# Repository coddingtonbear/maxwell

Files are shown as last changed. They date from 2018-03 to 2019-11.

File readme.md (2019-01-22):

# Maxwell: Bicycle Electrification



See my little blog post about this here: [http://coddingtonbear.net/maxwell-bicycle-electrification/](http://coddingtonbear.net/maxwell-bicycle-electrification/).

I have a bicycle dynamo on my bike, a rudimentary understanding of electronics, and a bunch of neopixels, gps, and bluetooth modules to use.  This is what happens when those things combine.

Maxwell is a two-part bike computer I've designed to allow me to do a few things:

* Light and control neopixel LEDs wrapped around my bike for added safety while biking at night, and added fun when biking with groups.
* Charge an easily-swappable 18650 Li-On cell for potential use when bike touring.
* Gather and transmit GPS coordinates for display on the internet somewhere.
* Display status information including my current speed, battery voltage, and current consumption, as well as disable or enable bike features including, most importantly, disabling and enabling the LEDs from a small screen mounted at the front of the bike.
* Send interesting data for display on the internet for completely impractical reasons.

The "remote" unit is based around the STM32F103CB microcontroller, and the "base" unit is based around its slightly-more-full-featured brother, the STM32F103RE.  Both communicate with one another over a CANBus (routed through two of the conductors in a length of ethernet cable) to share status information and emit/handle commands.




## Schematics

### Main





### LTE Module



### Head Unit (Remote)




## Errata

Checked items indicate errata that have been corrected in the schematic.

### Maxwell

None as of rev 1.7.

### Maxwell-remote

* [ ] Incorrect diode footprint for polarity protection.  There also might be a power deliver problem through those diodes.  Investigate that the selected mosftet is ON at Vgs -3.3.
* [ ] I think the gerbers I generated originally may have excluded the rear solder mask, as the resistors and vias were covered.
* [ ] Board-to-board interconnect should probably either not use an FPC connector, or use multiple conductors for power/ground.  I had to build a workaround connector for transferring power between the two boards.
* [ ] Resistor R2 of maxwell-remote-2 isn't really necessary; it could be connected directly to VCC.

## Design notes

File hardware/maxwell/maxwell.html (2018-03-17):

# BOM Rev

Date

Company

Comment 1

Comment 2

Comment 3

Comment 4

Total Parts

# 82 (Unique 56)

Ref

Qty

Value

Footprint

Datasheet

[BZ] -

BZ1

1

Buzzer

coddingtonbear/coddingtonbear.pretty:12mm_buzzer

[C] -

C1 C2 C3

3

2.2u

coddingtonbear:CP_Tantalum_Case-C_EIA-6032-28_Milling

C4 C5

2

0.1u

coddingtonbear/coddingtonbear.pretty:0805_Milling

C6 C7 C8 C9

4

22p

coddingtonbear/coddingtonbear.pretty:0805_Milling

C10 C11 C12 C13

4

100n

coddingtonbear/coddingtonbear.pretty:0805_Milling

C14

1

220u

coddingtonbear:CP_Tantalum_Case-C_EIA-6032-28_Milling

C15

1

100u

coddingtonbear:CP_Tantalum_Case-D_EIA-7343-31_Milling

C17

1

0.1

fruchti/fruchtilib/mod/rcl.pretty:CP_13mm_200

C18

1

100nF

coddingtonbear/coddingtonbear.pretty:0805_Milling

[D] -

D1

1

GS1M-LTP

mcous/kicad-lib/footprints/diode.pretty:DO-214AC

D2 D3

2

18

adamgreig/agg-kicad/agg.pretty:DO-214AA-SMB

D4

1

MB24S

coddingtonbear/coddingtonbear.pretty:SO-4_Milling

[J] -

J1

1

Canbus 1

coddingtonbear/coddingtonbear.pretty:JST_XH_B05B-XH-A_05x2.50mm_Straight_LargePads

J2

1

Canbus 2

coddingtonbear/coddingtonbear.pretty:JST_XH_B05B-XH-A_05x2.50mm_Straight_LargePads

J3

1

Neopixel

coddingtonbear/coddingtonbear.pretty:JST_XH_B03B-XH-A_03x2.50mm_Straight_LargePads

J4

1

BOOT0

coddingtonbear:Pin_Header_Straight_1x02_Pitch1.27mm_JMP

J5

1

SPI2_A

coddingtonbear/coddingtonbear.pretty:JST_XH_B06B-XH-A_06x2.50mm_Straight_LargePads

J6

1

Programmer

KiCad/Pin_Headers.pretty:Pin_Header_Straight_1x04_Pitch2.54mm

J7

1

Dynamo Input

coddingtonbear/coddingtonbear.pretty:JST_XH_B02B-XH-A_02x2.50mm_Straight_LargePads

J8

1

BOOT1

coddingtonbear:Pin_Header_Straight_1x02_Pitch1.27mm_JMP

J9

1

Battery

coddingtonbear/coddingtonbear.pretty:JST_XH_B02B-XH-A_02x2.50mm_Straight_LargePads

J10

1

SPI2_B

coddingtonbear/coddingtonbear.pretty:JST_XH_B06B-XH-A_06x2.50mm_Straight_LargePads

J11

1

BACKUP

coddingtonbear/coddingtonbear.pretty:JST_XH_B02B-XH-A_02x2.50mm_Straight_LargePads

J12

1

UART4

coddingtonbear/coddingtonbear.pretty:JST_XH_B04B-XH-A_04x2.50mm_Straight_LargePads

J13

1

UART5

coddingtonbear/coddingtonbear.pretty:JST_XH_B04B-XH-A_04x2.50mm_Straight_LargePads

J14

1

I2C1

coddingtonbear/coddingtonbear.pretty:JST_XH_B04B-XH-A_04x2.50mm_Straight_LargePads

J15

1

GPIO

KiCad/Pin_Headers.pretty:Pin_Header_Straight_1x03_Pitch2.54mm

[Q] -

Q1

1

BSS138

coddingtonbear/coddingtonbear.pretty:SOT-23_LargePads

Q2

1

PSMN5R4-25YLD

coddingtonbear/coddingtonbear.pretty:PSMN5R4-25YLD

Q3 Q4 Q5

3

NTR1P02T1

coddingtonbear/coddingtonbear.pretty:SOT-23_LargePads

[R] -

R1 R6 R7 R8 R10 R13 R28 R35

8

10k

coddingtonbear/coddingtonbear.pretty:0805_Milling

R2 R16

2

2.2k

coddingtonbear/coddingtonbear.pretty:0805_Milling

R3 R29 R31

3

330

coddingtonbear/coddingtonbear.pretty:0805_Milling

R4

1

>35

coddingtonbear/coddingtonbear.pretty:0805_Milling

R5 R9

2

100k

coddingtonbear/coddingtonbear.pretty:0805_Milling

R11

1

50

coddingtonbear/coddingtonbear.pretty:0805_Milling

R12

1

16-17k

coddingtonbear/coddingtonbear.pretty:0805_Milling

R14

1

200

coddingtonbear/coddingtonbear.pretty:0805_Milling

R19

1

2k

coddingtonbear/coddingtonbear.pretty:0805_Milling

R20 R21 R23 R24

4

ANY

coddingtonbear/coddingtonbear.pretty:0805_Milling

R22

1

0.02

coddingtonbear/coddingtonbear.pretty:0805_Milling

R33

1

1M

coddingtonbear/coddingtonbear.pretty:0805_Milling

R34

1

110k

coddingtonbear/coddingtonbear.pretty:0805_Milling

R37

1

120

coddingtonbear/coddingtonbear.pretty:0805_Milling

[U] -

U1

1

MCP1501

adamgreig/agg-kicad/agg.pretty:SOT-23-6

U2

1

SN65HVD233

adamgreig/agg-kicad/agg.pretty:SOIC-8

U3

1

ITEAD_HC-05

pelrun/libKiCad/footprint/w_rf_modules.pretty:ITEAD_HC-05

U5

1

ESP-32S

coddingtonbear/coddingtonbear.pretty:ESP-32S

U6

1

FGPMMOPA6C

coddingtonbear/coddingtonbear.pretty:FGPMMOPA6C

U7

1

STM32F103RETx

kicad-castellated-breakouts:QFP64-1.27MM-CASTELLATED

U8

1

TLP188

coddingtonbear/coddingtonbear.pretty:SO-4_Milling

U9

1

Buck Regulator

coddingtonbear/coddingtonbear.pretty:BOOST_LM2596_3A

U10

1

MIC39102

adamgreig/agg-kicad/agg.pretty:SOIC-8

[U*] -

U*NaN

1

MCP73831T

apexelectrix/apex-smd.pretty:SOT-23-5

[Y] -

Y1

1

32.768k

KiCad/Crystals.pretty:Crystal_SMD_SeikoEpson_MC306-4pin_8.0x3.2mm

Y2

1

8M

nqbit/NQBit.pretty:HC-49USX_SMD

# BOM made with KICAD_BOM_WIZARD (https://github.com/HashDefineElectronics/KiCad_BOM_Wizard) (Generated Thursday, March 01, 2018 'PMt' 10:14:26 PM)

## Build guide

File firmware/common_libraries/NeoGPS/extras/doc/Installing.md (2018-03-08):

Installing
==========

1. [Download the library](#1-download-the-library)
2. [Choose a serial port](#2-choose-a-serial-port)
3. [Connect the GPS device](#3-connect-the-gps-device)
4. [Review `GPSport.h`](#4-review-librariesneogpssrcgpsporth)
5. [Open the example](#5--open-the-example-sketch-nmeaino)
6. [Build and upload](#6--build-and-upload-the-sketch-to-your-arduino)
<hr>

### 1. Download the library

It is easiest to use the [Ardino IDE Library Manager](https://www.arduino.cc/en/Guide/Libraries#toc3) to automatically download and install NeoGPS.  Select the menu **Sketch -> Include Library -> Manage Libraries**.  Then type "NeoGPS" in the Search box.

If you need to perform a manual installation,:

* Download the [master ZIP file](https://github.com/SlashDevin/NeoGPS/archive/master.zip).
*  Open the zip file and open the nested `NeoGPS-master` subdirectory.
*  Select and copy all files in the `NeoGPS-master` subdirectory into a new `Arduino/Libraries/NeoGPS` directory, like most libraries.  The `Arduino/Libraries/NeoGPS` directory should contain:<br>
```
extras
examples
src
library.properties
LICENSE
README.md
```

<hr>

### 2. Choose a serial port

**BEST**: The fastest, most reliable way to connect a GPS device is to use a HardwareSerial port.

On any Arduino board, you can connect the GPS device to the `Serial` pins (0 & 1).  You can still print debug statements, and they will show up on the Serial Monitor window.  The received GPS characters will not interfere with those prints, and you will not see those characters on the Serial Monitor window.

However, when you need to upload a new sketch to the Arduino over USB, **you must disconnect the GPS TX from the Arduino RX pin 0.**  Otherwise, the GPS characters will interfere with the upload data.  Some people put a switch in that connection to make it easy to upload without disturbing the wires.

For Mega, Due and Teensy boards, you can connect the GPS device to the `Serial1`,  `Serial2` or `Serial3` pins.

For Micro and Leo (and other 32U4-based Arduinos), you can connect the GPS device to the `Serial1` pins.

**2nd Best**:  If you can't connect the GPS device to a `HardwareSerial` port, you should download and install the [AltSoftSerial](https://github.com/PaulStoffregen/AltSoftSerial) or [NeoICSerial](https://github.com/SlashDevin/NeoICSerial) library.  These libraries only work on two specific pins (8 & 9 on an UNO).  This library is very efficient and reliable.  It uses one of the hardware TIMERs, so it may conflict with libraries that use TIMERs or PWM output (e.g., servo).

**3rd Best**:  If you can't use the pins required by `AltSoftSerial`, and your GPS device runs at 9600, 19200 or 38400 baud, you should download and install the [NeoSWSerial](https://github.com/SlashDevin/NeoSWSerial) library.  This library is almost as efficient.  It will help you avoid common timing problems caused by `SoftwareSerial`.  It does not need an extra TIMER, so it can be used with most other libraries.  It does use Pin Change Interrupts, but there is an option in the header file that allows you to coordinate other PCI usage with `NeoSWSerial`.

`NeoSWSerial` can be used with `AltSoftSerial` at the same time, allowing your sketch to have two extra serial ports.

**WORST**:  `SoftwareSerial` is NOT RECOMMENDED, because it disables interrupts for long periods of time.  This can interfere with other parts of your sketch, or with other libraries.  It cannot transmit and receive at the same time, and your sketch can only receive from one `SoftwareSerial` instance at time.

<hr>

### 3. Connect the GPS device

Most GPS devices are 3.3V devices, and most Arduinos are 5V devices.  Although many GPS modules are described as "3V & 5V compatible", 

<p align=center><b>YOU SHOULD NOT CONNECT A 5V ARDUINO TRANSMIT PIN TO THE 3.3V GPS RX PIN</b></p>

This can damage the device, cause overheating, system power problems or decrease the lifetime of battery-operated systems.  You must level-shift this connection with inexpensive level-shifting modules (best) or a resistor divider.

Connecting the 3.3V GPS TX pin to a 5V Arduino receive pin will not damage the GPS device, but it may not be reliable.  This is because the GPS TX voltage is slightly lower than what the Arduino requires.  It works in many situations, but if you are not able to receive GPS characters reliably, you probably need to use a level-shifting module (best) or a diode+resistor to "pull up" the GPS TX pin voltage.

<hr>

### 4. Review `Libraries/NeoGPS/src/GPSport.h`

This file declares a the serial port to be used for the GPS device.  You can either:

* Use the default `GPSport.h` and connect your GPS device according to what it chooses; or
* Replace the entire contents of `GPSport.h` and insert your own declarations (see below and comments in `GPSport.h`).

#### Default choices for GPSport.h

By default, Mega, Leonardo, Due, Zero/MKR1000 and Teensy boards will use `Serial1`.

All other Boards will use [AltSoftSerial](https://github.com/PaulStoffregen/AltSoftSerial) on two specific pins (see table at linked page).

If you want to use a different serial port library (review step 2 above), you must edit these `#include` lines in `GPSport.h`:

```
  //#include <NeoHWSerial.h>    // NeoSerial or NeoSerial1 for INTERRUPT_PROCESSING
  #include <AltSoftSerial.h>    // <-- DEFAULT.  Two specific pins required (see docs)
  //#include <NeoICSerial.h>    // AltSoftSerial with Interrupt-style processing
  //#include <NeoSWSerial.h>    // Any pins, only @ 9600, 19200 or 38400 baud
  //#include <SoftwareSerial.h> // NOT RECOMMENDED!
```

Uncomment **one** of those include statements, and it will use that library for the GPS serial port.

If you uncomment the `NeoSWSerial.h` include, pins 3 and 4 will be used for the GPS.  If your GPS is on different pins, you must edit these `#define` lines in `GPSport.h`:

    #define RX_PIN 4
    #define TX_PIN 3

#### Choosing your own serial port

If you know what serial port you want to use, you can **REPLACE EVERYTHING** in `GPSport.h' with the three declarations that are used by all example programs: 

1. the `gpsPort` variable **(include its library header if needed)**;
2. the double-quoted C string for the `GPS_PORT_NAME` (displayed by all example programs); and
3. the `DEBUG_PORT` to use for Serial Monitor print messages (usually `Serial`).

All the example programs can use any of the following serial port types:

* HardwareSerial (built-in `Serial`, `Serial1` et al. STRONGLY recommended)
* [AltSoftSerial](https://github.com/PaulStoffregen/AltSoftSerial) **DEFAULT** (only works on one specific Input Capture pin)
* [NeoICSerial](https://github.com/SlashDevin/NeoICSerial) (only works on one specific Input Capture pin)
* [NeoHWSerial](https://github.com/SlashDevin/NeoHWSerial) (required for NMEA_isr and NMEASDlog on built-in serial ports)
* [NeoSWSerial](https://github.com/SlashDevin/NeoSWSerial) (works on most pins)
* SoftwareSerial (built-in, NOT recommended)

Be sure to download the library you have selected (NOTE: `HardwareSerial` and `SoftwareSerial` are pre-installed by the Arduino IDE and do not need to be downloaded).

For example, to make all examples use `Serial` for the GPS port **and** for Serial Monitor messages, `GPSport.h` should contain just these 3 declarations:

```
#ifndef GPSport_h
#define GPSport_h

#define gpsPort Serial
#define GPS_PORT_NAME "Serial"
#define DEBUG_PORT Serial

#endif
```

Or, to make all examples use `AltSoftSerial` for the GPS port and `Serial` for Serial Monitor messages, `GPSport.h` should contain just these statements:

```
#ifndef GPSport_h
#define GPSport_h

#include <AltSoftSerial.h>
AltSoftSerial gpsPort;
#define GPS_PORT_NAME "AltSoftSerial"
#define DEBUG_PORT Serial

#endif
```

<hr>

### 5.  Open the example sketch NMEA.ino

In the Arduino IDE, select **File -> Examples -> NeoGPS -> NMEA**.

<hr>

### 6.  Build and upload the sketch to your Arduino.

**Note:**  If the sketch does not compile, please see the [Troubleshooting](Troubleshooting.md#configuration-errors) section.

When the sketch begins, you should see this:
```
NMEA.INO: started
  fix object size = 31
  gps object size = 84
Looking for GPS device on Serial1

GPS quiet time is assumed to begin after a RMC sentence is received.
  You should confirm this with NMEAorder.ino

Status,UTC Date/Time,Lat,Lon,Hdg,Spd,Alt,Sats,Rx ok,Rx err,Rx chars,
3,2016-05-24 01:21:29.00,472852332,85652650,,138,,,1,0,66,
3,2016-05-24 01:21:30.00,472852311,85652653,,220,24040,7,9,0,557,
3,2016-05-24 01:21:31.00,472852315,85652647,,449,24080,7,17,0,1048,
  etc.
```
The default NeoGPS configuration is **Nominal**, as described [here](Configurations.md#typical-configurations).  If you do not see this output, please review the  [Troubleshooting](Troubleshooting.md#gps-device-connection-problems) section.

This output can be copy & pasted into a into a text editor for saving as a CSV file, which can then be imported into a spreadsheet program for graphing or analysis.

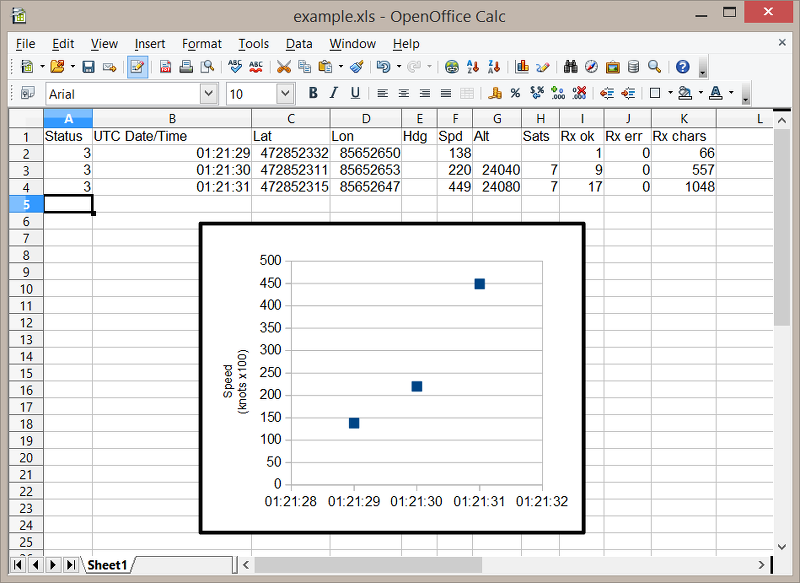
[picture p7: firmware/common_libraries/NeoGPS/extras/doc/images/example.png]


<hr>

### The NMEA.ino example works!
Once you have verified the GPS device connection and build process with this first example, you should also verify your device's behavior with `NMEAorder.ino` (see [this section](Troubleshooting.md#quiet-time-interval)).  This can avoid problems later on, when you start adding/merging other functions to do your "work".

[Other examples](Examples.md) include `NMEAloc.ino`, which shows how to use just the location fields of a fix, or `NMEAtimezone.ino`, which shows how to adjust the GPS time for your local time zone.

If you are logging information to an SD card, you should next try `NMEA_isr.ino`.  It is identical to `NMEA.ino`, except that it handles the GPS characters during the RX char interrupt.  Interrupt handling will require one of the NeoXXSerial libraries to be installed (e.g. [NeoHWSerial](https://github.com/SlashDevin/NeoHWSerial)).

If you are working on a drone or other autonomous system, you should you should read about [Coherency](Coherency.md) and the interrupt-driven technique in [NMEA_isr](/examples/NMEA_isr/NMEA_isr.ino).

You can also try other configurations.  Please see [Choosing Your Configuration](Choosing.md) for more information, and then simply edit `GPSfix_cfg.h` and/or `NMEAGPS_cfg.h`, or select an [example configuration](../configs) and copy these three files into your application directory: `NeoGPS_cfg.h`, `GPSfix_cfg.h`, and `NMEAGPS_cfg.h`.

You can review and edit each of the copied configuration files to add or remove messages or fields, at any time.

**Note:**  Not all configurations will work with all example applications.  Compiler error messages are emitted for incompatible settings, or if an example requires certain configurations.

### I have a ublox GPS device
After you have tried all the standard NMEA examples, and you need the ublox-specific capabilities of NeoGPS, please see the [ublox](ublox.md) section.  Try `PUBX.ino` first, then try `ublox.ino` if you *really* need the binary protocol.

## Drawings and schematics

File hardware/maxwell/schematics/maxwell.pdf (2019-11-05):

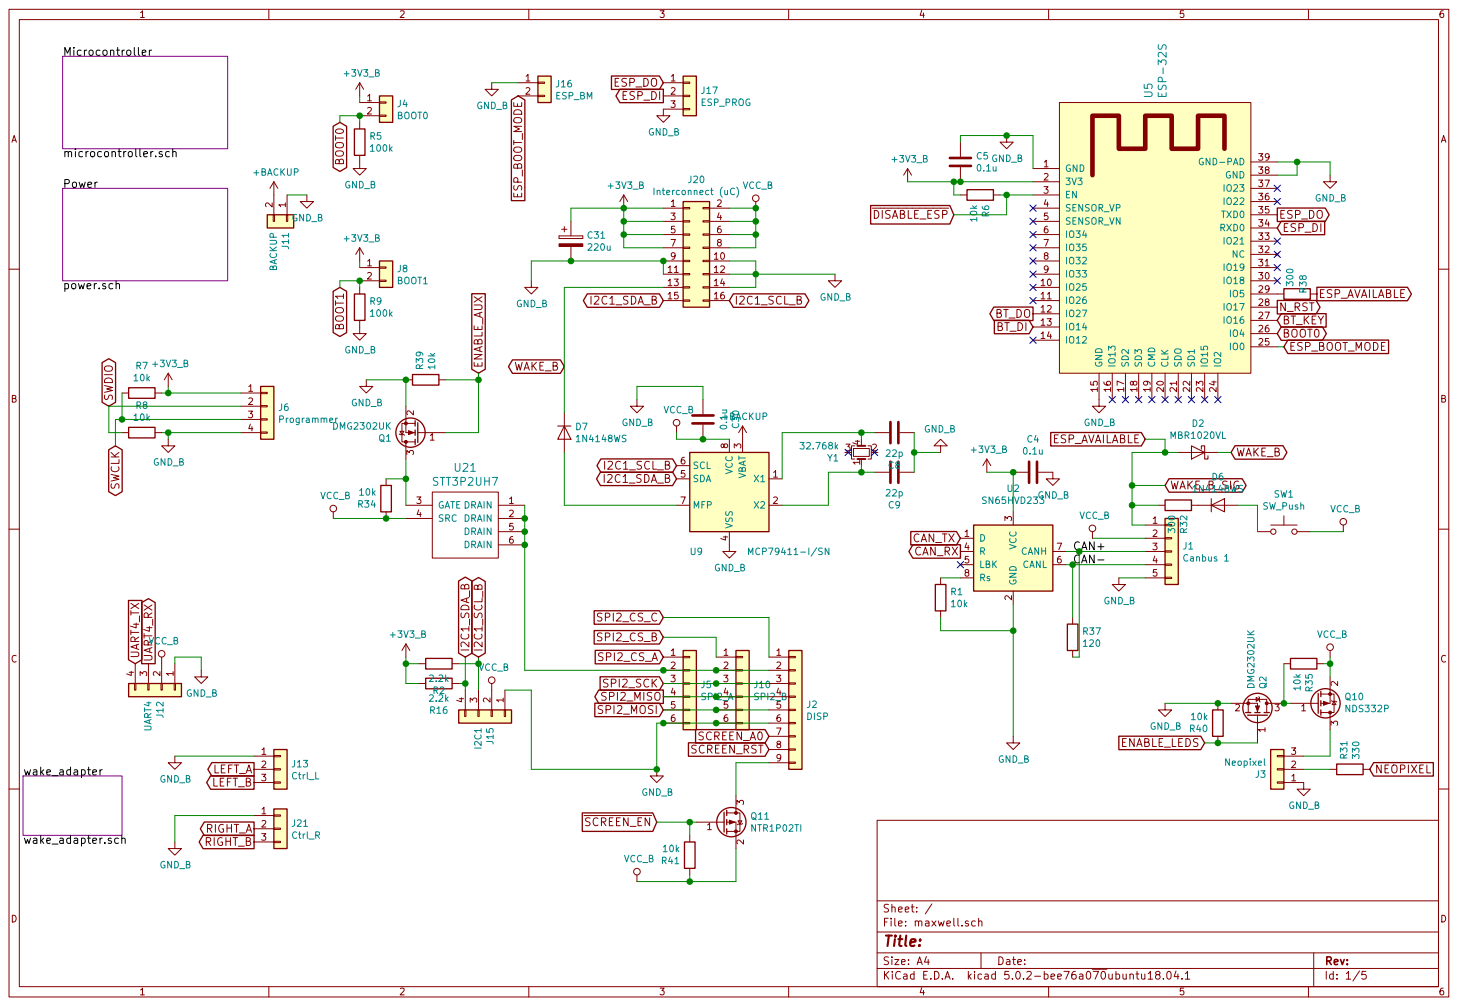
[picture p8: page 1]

Id: 1/5 Title: File: maxwell.sch Sheet: / BOOT1

4 SDA 5 SCL 6 MFP 7 VCC

J5SPI2_A 4 | 4

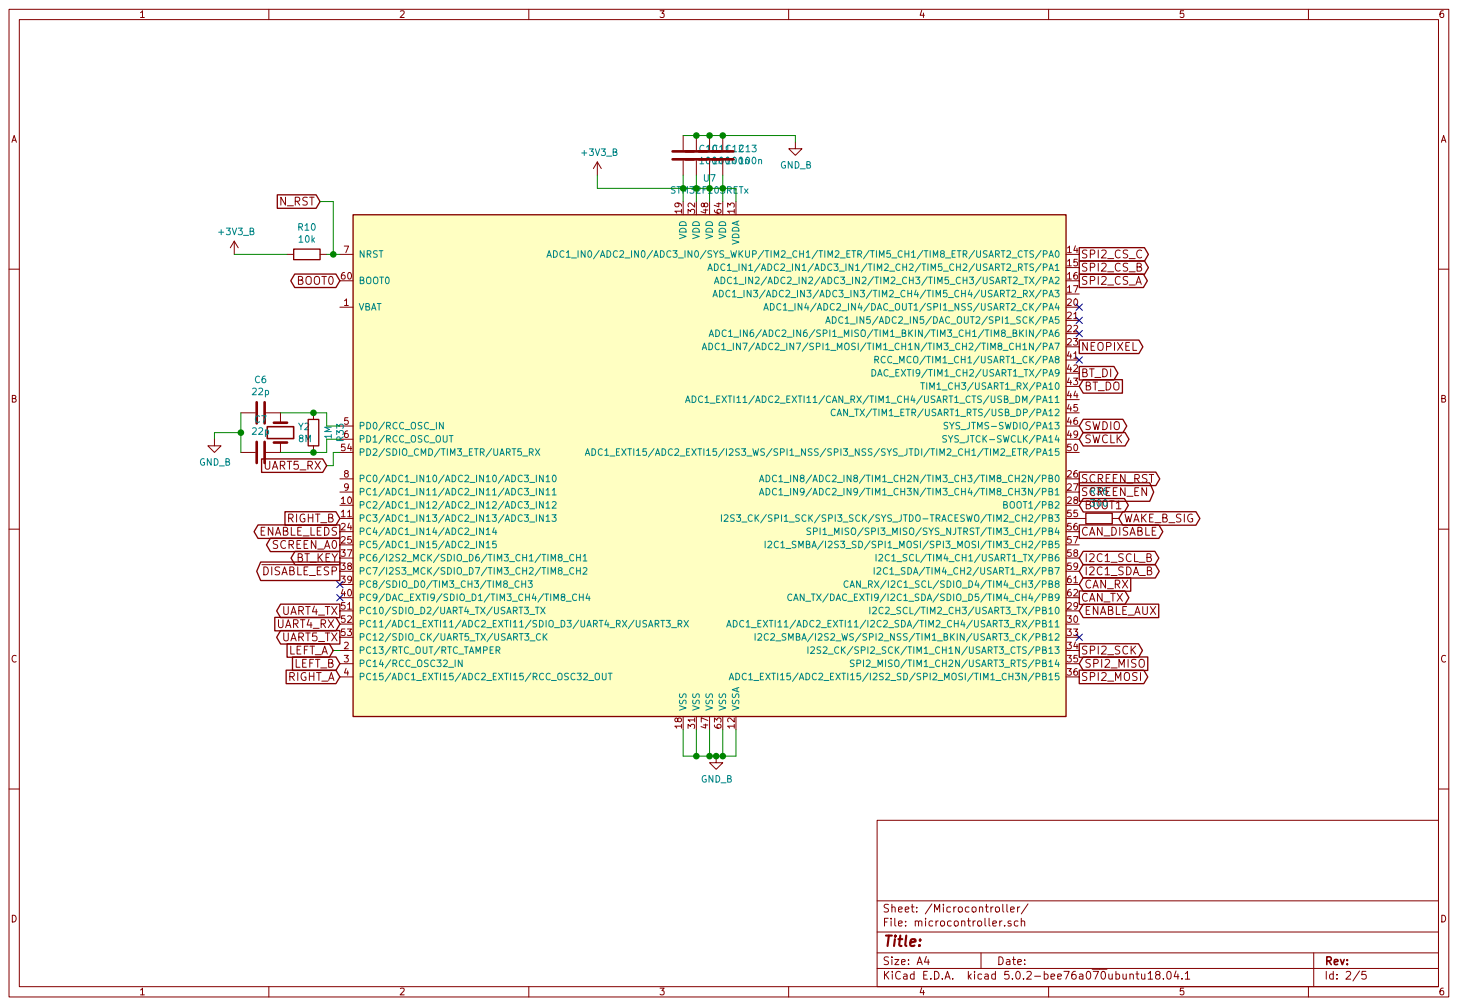
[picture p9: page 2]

Id: 2/5 Title: File: microcontroller.sch Sheet: /Microcontroller/

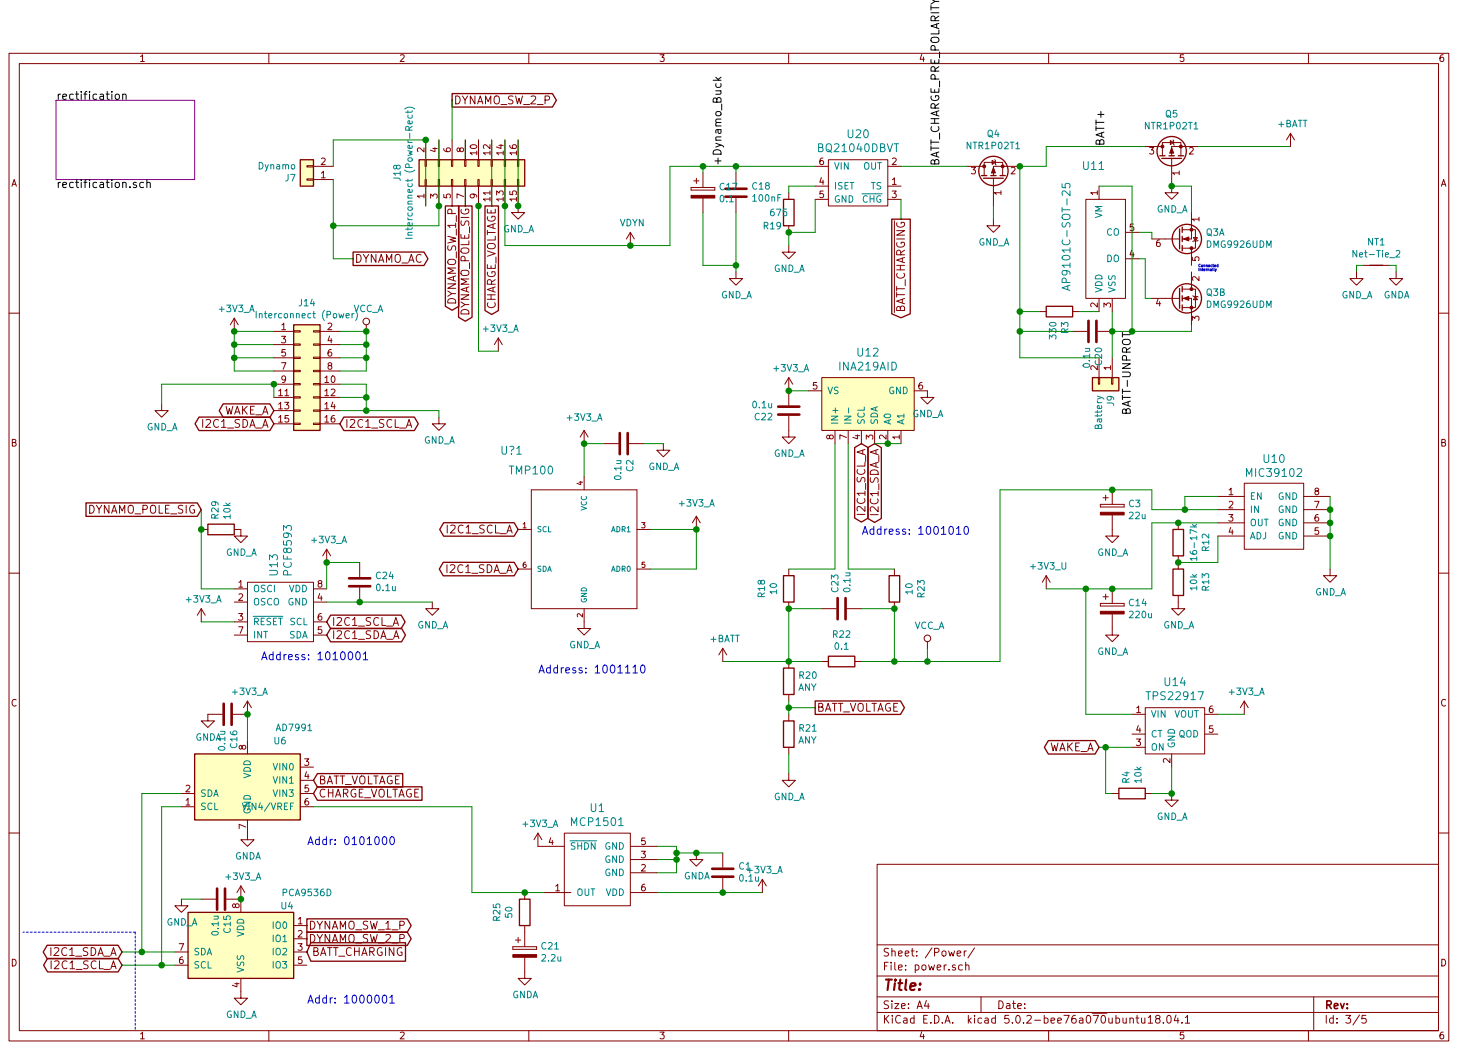
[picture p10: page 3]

3 DO 4 CO 5 U11 AP9101C-SOT-25 Connected

4 VS 5 GND 6 IN- 7 IN+

4 ADR0 5 SDA 6 U?1TMP100 OUT 1 GND 2 GND 3 SHDN 4 GND 5 VDD 6 U1 MCP1501

2 ON 3 CT 4 QOD 5 VOUT 6 U14 TPS22917

File: power.sch Sheet: /Power/
Id: 3/5 Title:

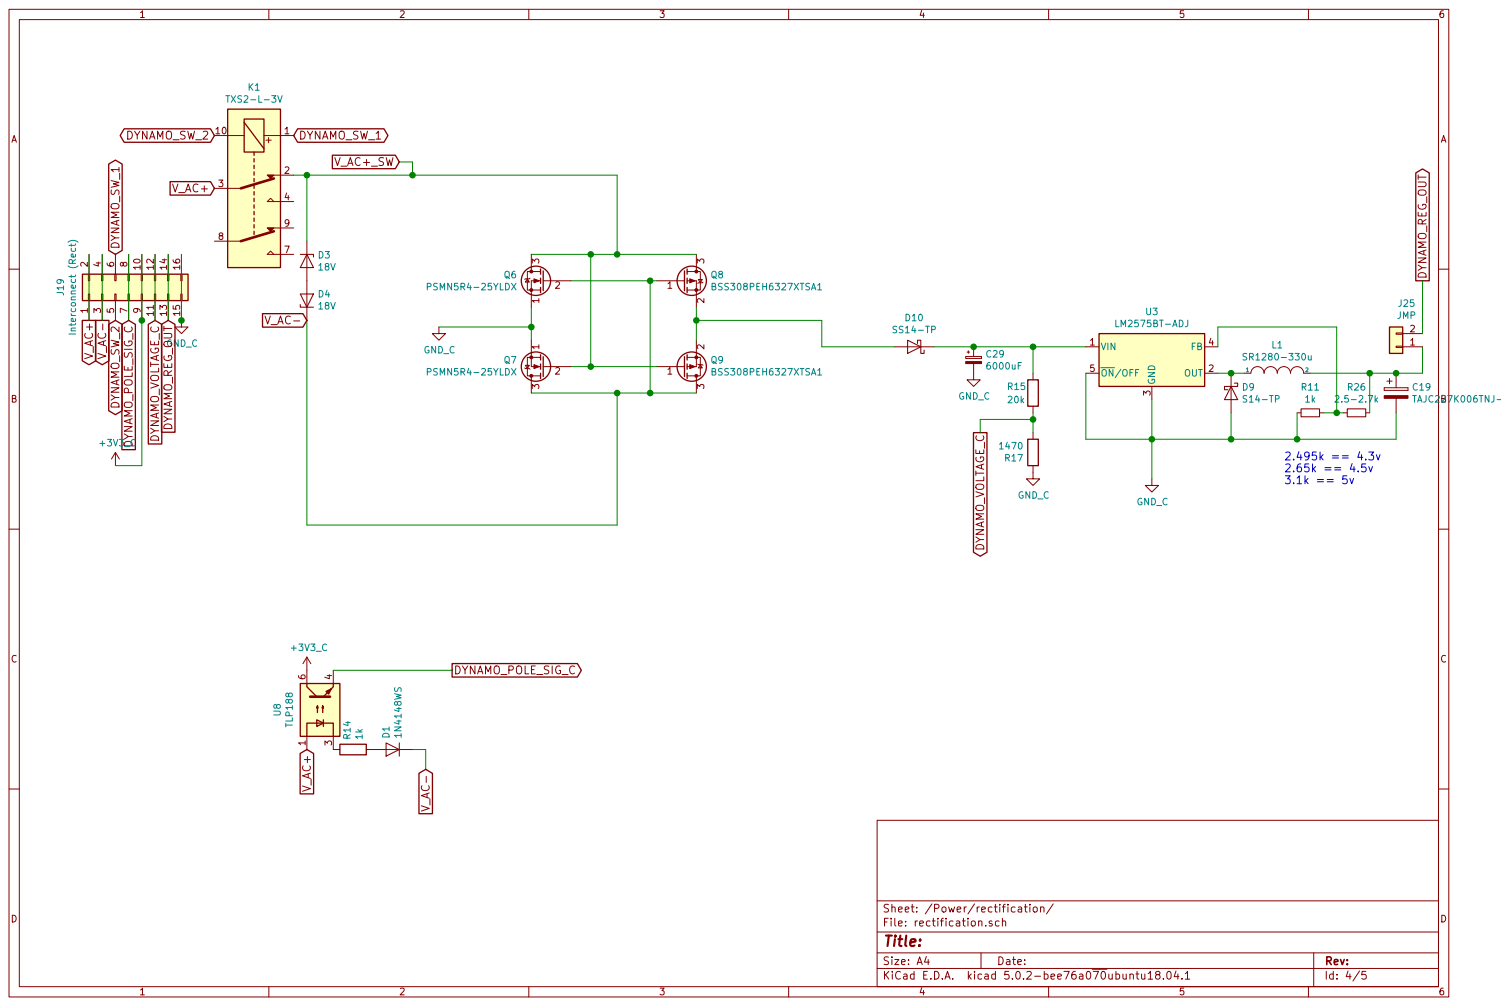
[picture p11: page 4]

Id: 4/5 Title: File: rectification.sch Sheet: /Power/rectification/

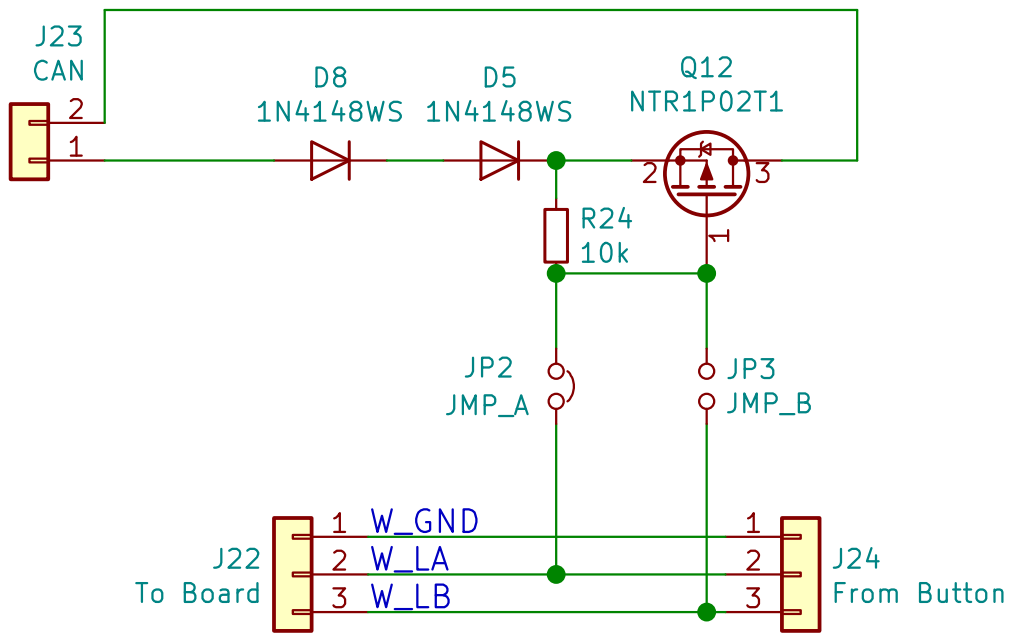
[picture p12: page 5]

2 W_LA | 2
W_LB 3 | 3

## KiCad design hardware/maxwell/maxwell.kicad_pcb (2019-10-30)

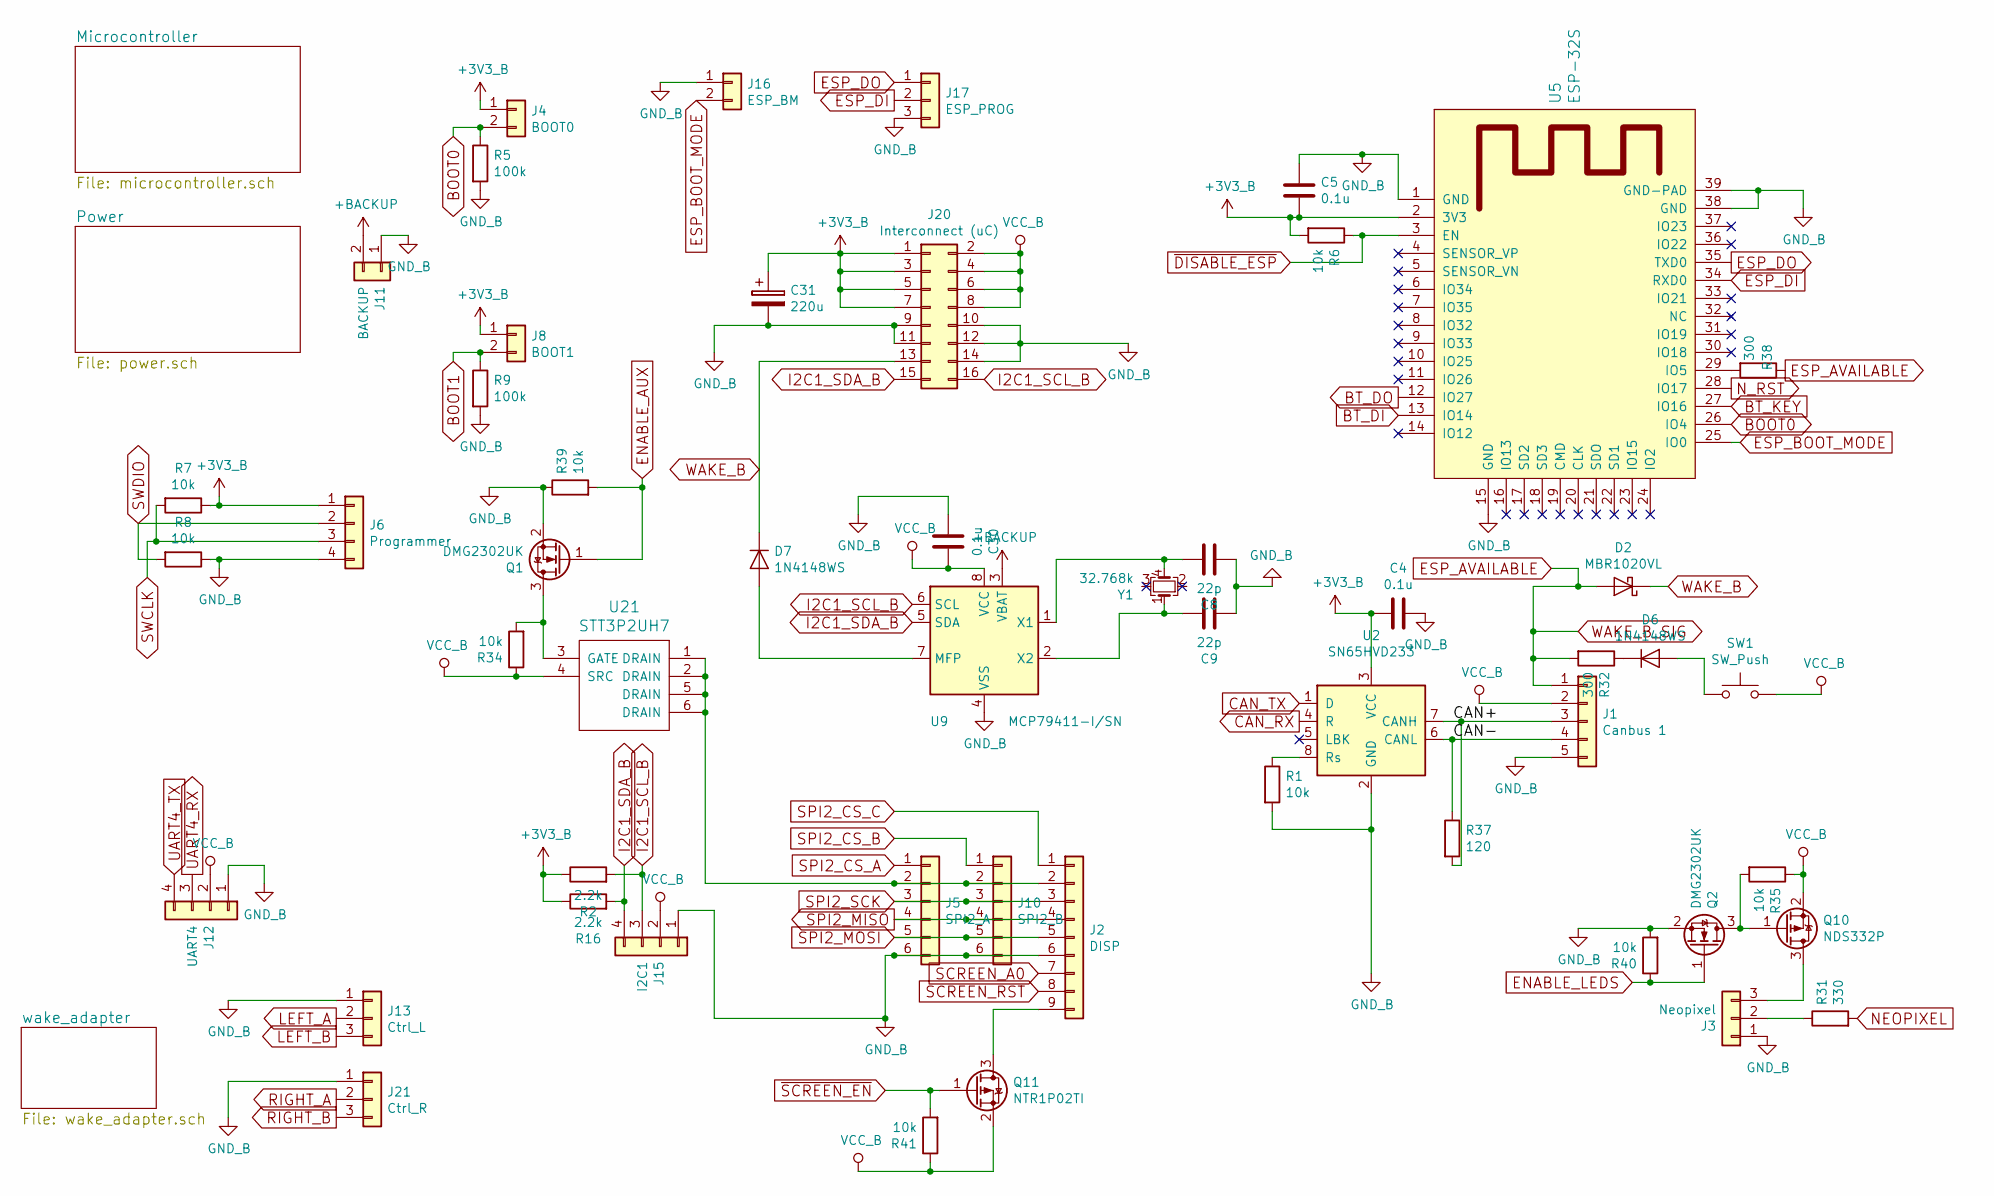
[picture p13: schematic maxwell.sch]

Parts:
C4, C5, C30: 0.1u; 0805_Milling
C8, C9: 22p; 0805_Milling
C31: 220u; CP_Tantalum_Case-C_EIA-6032-28_Milling
D2: MBR1020VL; D_SOD-123_LargePads
D6, D7: 1N4148WS; D_SOD-323_HandSoldering
J1: Canbus 1; JST_XH_B05B-XH-A_05x2.50mm_Straight_LargePads
J2: DISP; JST_XH_B09B-XH-A_1x09_P2.50mm_Straight_LargePads
J3: Neopixel; JST_XH_B03B-XH-A_03x2.50mm_Straight_LargePads
J4: BOOT0; Pin_Header_Straight_1x02_Pitch1.27mm_JMP
J5: SPI2_A; JST_XH_B06B-XH-A_06x2.50mm_Straight_LargePads
J6: Programmer; Pin_Header_Straight_1x04_Pitch2.54mm_LargePads
J8: BOOT1; Pin_Header_Straight_1x02_Pitch1.27mm_JMP
J10: SPI2_B; JST_XH_B06B-XH-A_06x2.50mm_Straight_LargePads
J11: BACKUP; JST_XH_B02B-XH-A_02x2.50mm_Straight_LargePads
J12: UART4; JST_XH_B04B-XH-A_04x2.50mm_Straight_LargePads
J13: Ctrl_L; JST_XH_B03B-XH-A_03x2.50mm_Straight_LargePads
J15: I2C1; JST_XH_B04B-XH-A_04x2.50mm_Straight_LargePads
J16: ESP_BM; Pin_Header_Straight_1x02_Pitch1.27mm_JMP
J17: ESP_PROG; JST_XH_B03B-XH-A_03x2.50mm_Straight_LargePads
J20: Interconnect (uC); IDC-Header_2x08_P2.54mm_Vertical_Largepads
J21: Ctrl_R; JST_XH_B03B-XH-A_03x2.50mm_Straight_LargePads
Q1, Q2: DMG2302UK; SOT-23_LargePads
Q10: NDS332P; SOT-23_LargePads
Q11: NTR1P02TI; SOT-23_LargePads
R1, R6, R7, R8, R34, R35, R39, R40, R41: 10k; 0805_Milling
R2, R16: 2.2k; 0805_Milling
R5, R9: 100k; 0805_Milling
R31: 330; 0805_Milling
R32, R38: 300; 0805_Milling
R37: 120; 0805_Milling
SW1: SW_Push; SMD_MINI_BLACK_TACTILE_SWITCH
U2: SN65HVD233; SOIC-8_3.9x4.9mm_P1.27mm_LargePads
U5: ESP-32S
U9: MCP79411-I/SN; SOIC-8_3.9x4.9mm_P1.27mm_LargePads
U21: STT3P2UH7; SOT-23-6_Handsoldering
Y1: 32.768k; Crystal_SMD_SeikoEpson_MC306-4Pin_8.0x3.2mm_HandSoldering

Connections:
+3V3_B: C4.2, C5.2, C31.1, J4.1, J6.1, J8.1, J20.1, J20.3, J20.5, J20.7, R2.1, R6.2, R7.1, R16.1, U2.3 (VCC), U5.2 (3V3); also elsewhere on the board
+BACKUP: J11.2, U9.3 (VBAT)
/CAN+: J1.3, R37.2, U2.7 (CANH)
/CAN-: J1.4, R37.1, U2.6 (CANL)
BOOT0: J4.2, R5.1, U5.26 (IO4); also elsewhere on the board
BOOT1: J8.2, R9.1; also elsewhere on the board
BT_DI: U5.13 (IO14); also elsewhere on the board
BT_DO: U5.12 (IO27); also elsewhere on the board
BT_KEY: U5.27 (IO16); also elsewhere on the board
CAN_RX: U2.4 (R); also elsewhere on the board
CAN_TX: U2.1 (D); also elsewhere on the board
ENABLE_AUX: Q1.1 (G), R39.2; also elsewhere on the board
ENABLE_LEDS: Q2.1 (G), R40.1; also elsewhere on the board
ESP_AVAILABLE: D2.2 (A), J1.1, R32.2, R38.1; also elsewhere on the board
ESP_BOOT_MODE: J16.2, U5.25 (IO0)
ESP_DI: J17.2, U5.34 (RXD0)
ESP_DO: J17.1, U5.35 (TXD0)
GND_B: C4.1, C5.1, C8.2, C9.2, C30.2, C31.2, J1.5, J2.6, J3.1, J5.6, J6.4, J10.6, J11.1, J12.1, J13.1, J15.1, J16.1, J17.3, J20.9, J20.10, J20.11, J20.12, J20.14, J21.1, Q1.2 (S), Q2.2 (S), R1.2, R5.2, R8.1, R9.2, R39.1, R40.2, U2.2 (GND), U5.1 (GND), U5.15 (GND), U5.38 (GND), U5.39 (GND-PAD), U9.4 (VSS); also elsewhere on the board
I2C1_SCL_B: J15.3, J20.16, R2.2, U9.6 (SCL); also elsewhere on the board
I2C1_SDA_B: J15.4, J20.15, R16.2, U9.5 (SDA); also elsewhere on the board
LEFT_A: J13.2; also elsewhere on the board
LEFT_B: J13.3; also elsewhere on the board
NEOPIXEL: R31.2; also elsewhere on the board
N_RST: U5.28 (IO17); also elsewhere on the board
unnamed: C8.1, U9.1 (X1), Y1.4
unnamed: C9.1, U9.2 (X2), Y1.1
unnamed: D6.1 (K), R32.1
unnamed: D6.2 (A), SW1.1
unnamed: D7.2 (A), U9.7 (MFP)
unnamed: J2.9, Q11.3 (D)
unnamed: J3.2, R31.1
unnamed: J3.3, Q10.3 (D)
unnamed: J2.2, J5.2, J10.2, U21.1 (DRAIN), U21.2 (DRAIN), U21.5 (DRAIN), U21.6 (DRAIN)
unnamed: Q1.3 (D), R34.2, U21.3 (GATE)
unnamed: Q2.3 (D), Q10.1 (G), R35.2
unnamed: R1.1, U2.8 (Rs)
unnamed: R38.2, U5.29 (IO5)
RIGHT_A: J21.2; also elsewhere on the board
RIGHT_B: J21.3; also elsewhere on the board
SCREEN_A0: J2.7; also elsewhere on the board
SCREEN_RST: J2.8; also elsewhere on the board
SPI2_CS_A: J5.1; also elsewhere on the board
SPI2_CS_B: J10.1; also elsewhere on the board
SPI2_CS_C: J2.1; also elsewhere on the board
SPI2_MISO: J2.4, J5.4, J10.4; also elsewhere on the board
SPI2_MOSI: J2.5, J5.5, J10.5; also elsewhere on the board
SPI2_SCK: J2.3, J5.3, J10.3; also elsewhere on the board
SWCLK: J6.3, R7.2; also elsewhere on the board
SWDIO: J6.2, R8.2; also elsewhere on the board
UART4_RX: J12.3; also elsewhere on the board
UART4_TX: J12.4; also elsewhere on the board
VCC_B: C30.1, J1.2, J12.2, J15.2, J20.2, J20.4, J20.6, J20.8, Q10.2 (S), Q11.2 (S), R34.1, R35.1, R41.1, SW1.2, U9.8 (VCC), U21.4 (SRC)
WAKE_B: D2.1 (K), D7.1 (K), J20.13
~DISABLE_ESP: R6.1, U5.3 (EN); also elsewhere on the board
~SCREEN_EN: Q11.1 (G), R41.2; also elsewhere on the board

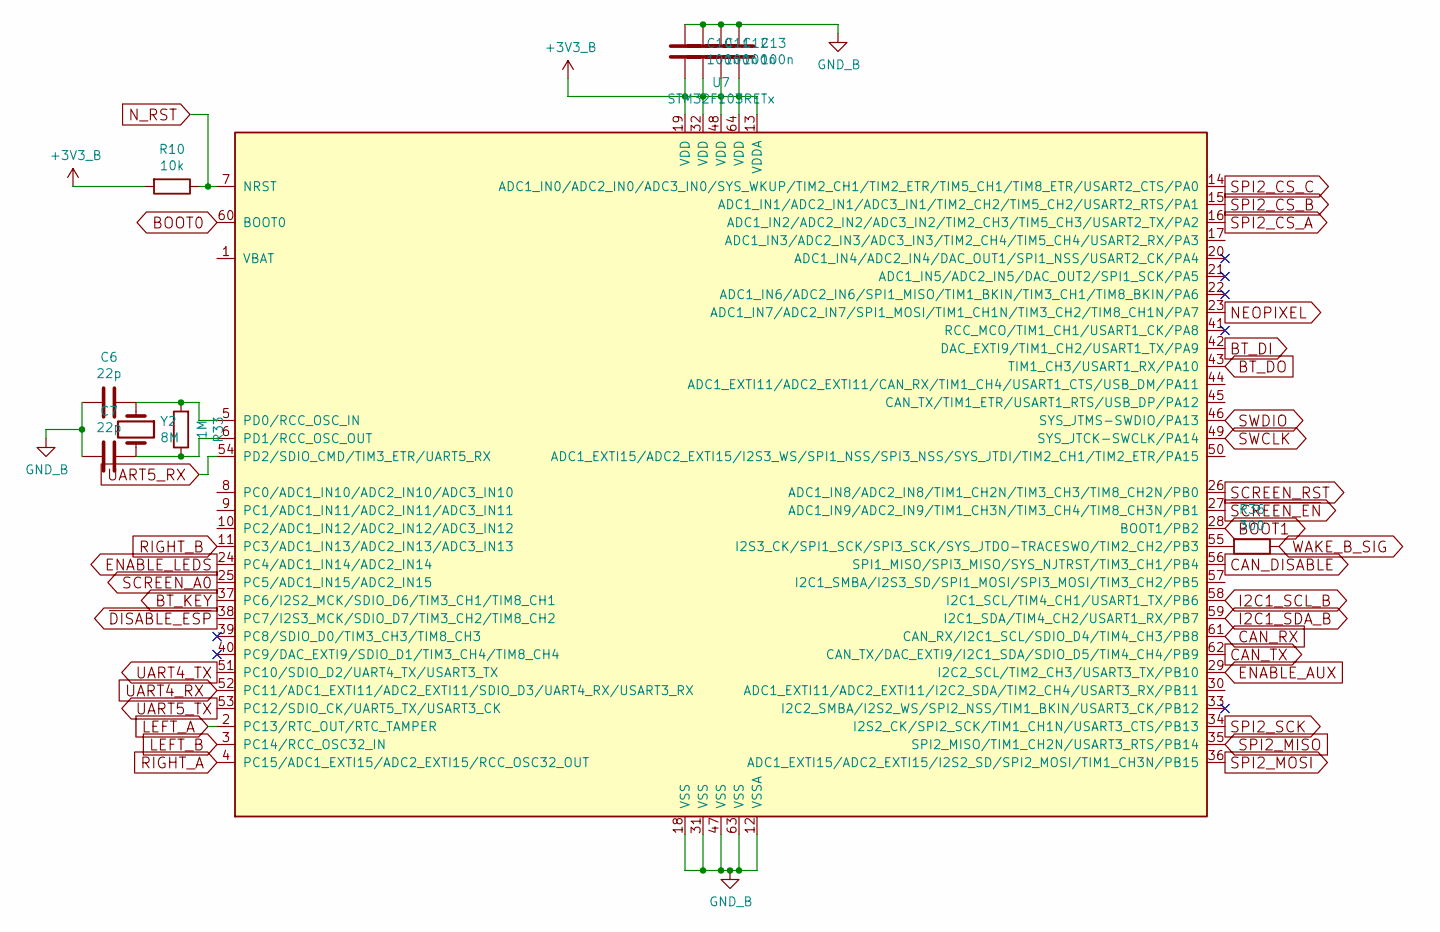
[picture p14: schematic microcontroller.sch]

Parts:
C6, C7: 22p; 0805_Milling
C10, C11, C12, C13: 100n; 0805_Milling
R10: 10k; 0805_Milling
R33: 1M; 0805_Milling
R36: 300; 0805_Milling
U7: STM32F103RETx; QFP64-1.27MM-CASTELLATED
Y2: 8M; Abracon-ABM2_LargePads

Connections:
+3V3_B: C10.1, C11.1, C12.1, C13.1, R10.2, U7.13 (VDDA), U7.19 (VDD), U7.32 (VDD), U7.48 (VDD), U7.64 (VDD); also elsewhere on the board
BOOT0: U7.60 (BOOT0); also elsewhere on the board
BOOT1: U7.28 (BOOT1/PB2); also elsewhere on the board
BT_DI: U7.42 (DAC_EXTI9/TIM1_CH2/USART1_TX/PA9); also elsewhere on the board
BT_DO: U7.43 (TIM1_CH3/USART1_RX/PA10); also elsewhere on the board
BT_KEY: U7.37 (PC6/I2S2_MCK/SDIO_D6/TIM3_CH1/TIM8_CH1); also elsewhere on the board
CAN_DISABLE: U7.56 (SPI1_MISO/SPI3_MISO/SYS_NJTRST/TIM3_CH1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)
CAN_RX: U7.61 (CAN_RX/I2C1_SCL/SDIO_D4/TIM4_CH3/PB8); also elsewhere on the board
CAN_TX: U7.62 (CAN_TX/DAC_EXTI9/I2C1_SDA/SDIO_D5/TIM4_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); also elsewhere on the board
ENABLE_AUX: U7.29 (I2C2_SCL/TIM2_CH3/USART3_TX/PB10); also elsewhere on the board
ENABLE_LEDS: U7.24 (PC4/ADC1_IN14/ADC2_IN14); also elsewhere on the board
ESP_AVAILABLE: R36.1; also elsewhere on the board
GND_B: C6.2, C7.2, C10.2, C11.2, C12.2, C13.2, U7.12 (VSSA), U7.18 (VSS), U7.31 (VSS), U7.47 (VSS), U7.63 (VSS); also elsewhere on the board
I2C1_SCL_B: U7.58 (I2C1_SCL/TIM4_CH1/USART1_TX/PB6); also elsewhere on the board
I2C1_SDA_B: U7.59 (I2C1_SDA/TIM4_CH2/USART1_RX/PB7); also elsewhere on the board
LEFT_A: U7.2 (PC13/RTC_OUT/RTC_TAMPER); also elsewhere on the board
LEFT_B: U7.3 (PC14/RCC_OSC32_IN); also elsewhere on the board
NEOPIXEL: U7.23 (ADC1_IN7/ADC2_IN7/SPI1_MOSI/TIM1_CH1N/T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); also elsewhere on the board
N_RST: R10.1, U7.7 (NRST); also elsewhere on the board
unnamed: C6.1, R33.2, U7.5 (PD0/RCC_OSC_IN), Y2.1
unnamed: C7.1, R33.1, U7.6 (PD1/RCC_OSC_OUT), Y2.2
unnamed: R36.2, U7.55 (I2S3_CK/SPI1_SCK/SPI3_SCK/SYS_JTDO-TRAC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)
RIGHT_A: U7.4 (PC15/ADC1_EXTI15/ADC2_EXTI15/RCC_OSC32_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); also elsewhere on the board
RIGHT_B: U7.11 (PC3/ADC1_IN13/ADC2_IN13/ADC3_IN13); also elsewhere on the board
SCREEN_A0: U7.25 (PC5/ADC1_IN15/ADC2_IN15); also elsewhere on the board
SCREEN_RST: U7.26 (ADC1_IN8/ADC2_IN8/TIM1_CH2N/TIM3_CH3/TI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); also elsewhere on the board
SPI2_CS_A: U7.16 (ADC1_IN2/ADC2_IN2/ADC3_IN2/TIM2_CH3/TIM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); also elsewhere on the board
SPI2_CS_B: U7.15 (ADC1_IN1/ADC2_IN1/ADC3_IN1/TIM2_CH2/TIM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); also elsewhere on the board
SPI2_CS_C: U7.14 (ADC1_IN0/ADC2_IN0/ADC3_IN0/SYS_WKUP/TIM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); also elsewhere on the board
SPI2_MISO: U7.35 (SPI2_MISO/TIM1_CH2N/USART3_RTS/PB14); also elsewhere on the board
SPI2_MOSI: U7.36 (ADC1_EXTI15/ADC2_EXTI15/I2S2_SD/SPI2_MO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); also elsewhere on the board
SPI2_SCK: U7.34 (I2S2_CK/SPI2_SCK/TIM1_CH1N/USART3_CTS/P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); also elsewhere on the board
SWCLK: U7.49 (SYS_JTCK-SWCLK/PA14); also elsewhere on the board
SWDIO: U7.46 (SYS_JTMS-SWDIO/PA13); also elsewhere on the board
UART4_RX: U7.52 (PC11/ADC1_EXTI11/ADC2_EXTI11/SDIO_D3/UA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); also elsewhere on the board
UART4_TX: U7.51 (PC10/SDIO_D2/UART4_TX/USART3_TX); also elsewhere on the board
UART5_RX: U7.54 (PD2/SDIO_CMD/TIM3_ETR/UART5_RX)
UART5_TX: U7.53 (PC12/SDIO_CK/UART5_TX/USART3_CK)
~DISABLE_ESP: U7.38 (PC7/I2S3_MCK/SDIO_D7/TIM3_CH2/TIM8_CH2); also elsewhere on the board
~SCREEN_EN: U7.27 (ADC1_IN9/ADC2_IN9/TIM1_CH3N/TIM3_CH4/TI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); also elsewhere on the board

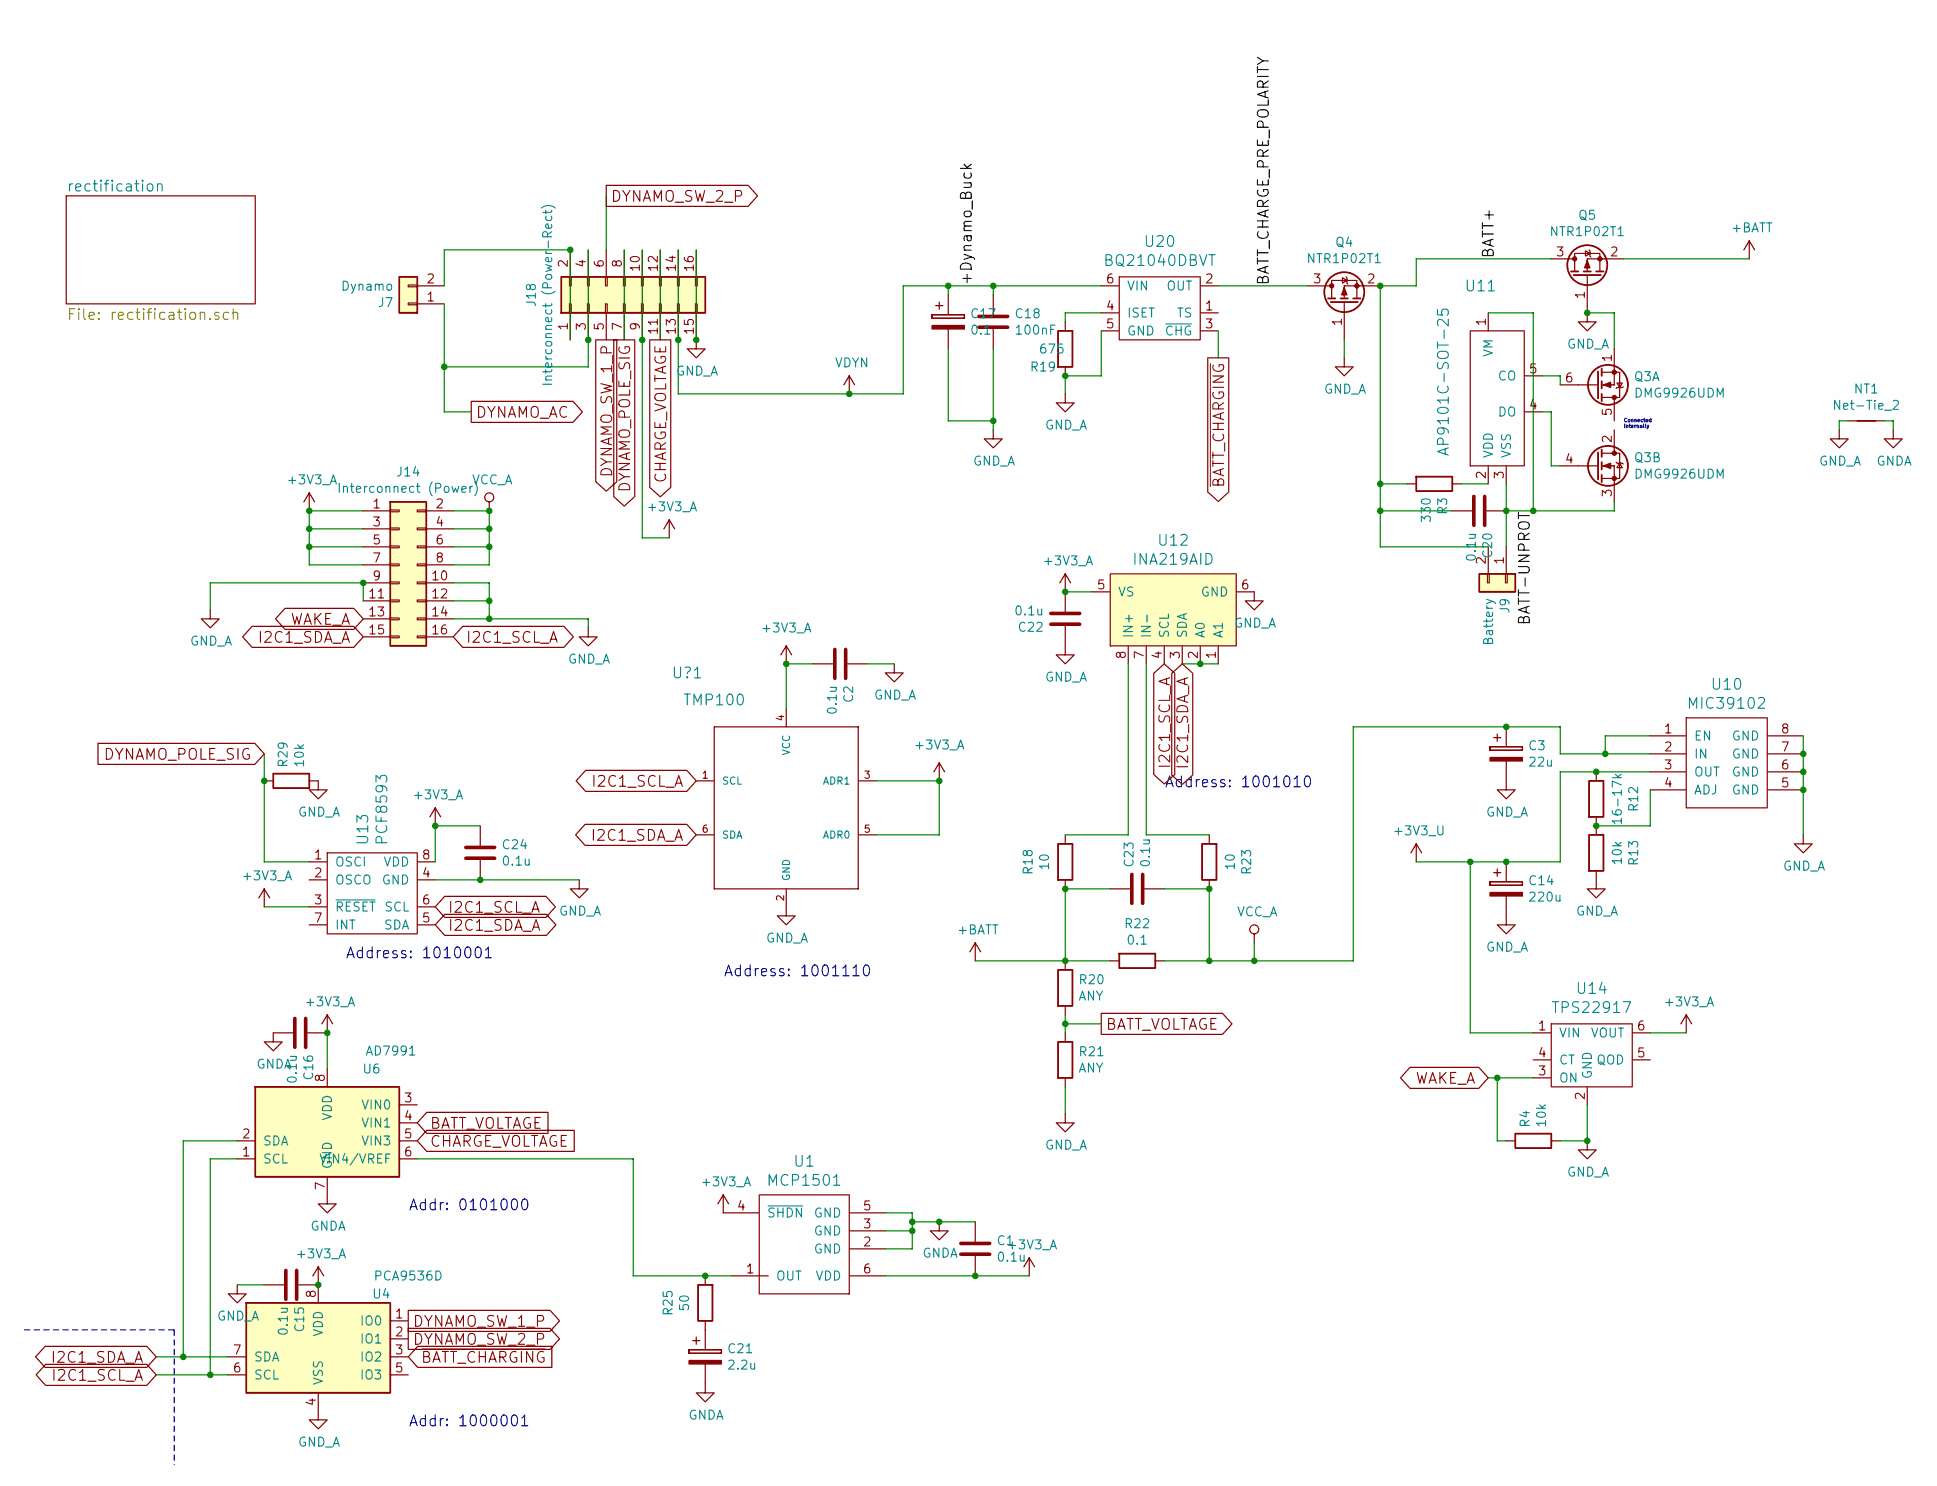
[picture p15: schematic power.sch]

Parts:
C1, C2, C15, C16, C20, C22, C23, C24: 0.1u; 0805_Milling
C3: 22u; CP_Tantalum_Case-C_EIA-6032-28_Milling
C14: 220u; CP_Tantalum_Case-C_EIA-6032-28_Milling
C17: 0.1; JST_XH_B02B-XH-A_02x2.50mm_Straight_LargePads
C18: 100nF; 0805_Milling
C21: 2.2u; CP_Tantalum_Case-C_EIA-6032-28_Milling
J7: Dynamo; JST_XH_B02B-XH-A_02x2.50mm_Straight_LargePads
J9: Battery; JST_XH_B02B-XH-A_02x2.50mm_Straight_LargePads
J14: Interconnect (Power); IDC-Header_2x08_P2.54mm_Vertical_Largepads
J18: Interconnect (Power-Rect); PinHeader_2x08_P2.54mm_Vertical_LargePads
NT1: Net-Tie_2; NetTie-2_SMD_Pad0.5mm
Q3: DMG9926UDM; SOT-23-6_Handsoldering
Q4, Q5: NTR1P02T1; SOT-23_LargePads
R3: 330; 0805_Milling
R4, R13, R29: 10k; 0805_Milling
R12: 16-17k; 0805_Milling
R18, R23: 10; 0805_Milling
R19: 675; 0805_Milling
R20, R21: ANY; 0805_Milling
R22: 0.1; 0805_Milling
R25: 50; 0805_Milling
U1: MCP1501; TSOT-23-6_HandSoldering
U4: PCA9536D; SOIC-8_3.9x4.9mm_P1.27mm_LargePads
U6: AD7991; SOT-23-8_Handsoldering
U10: MIC39102; SOIC-8_3.9x4.9mm_P1.27mm_LargePads
U11: AP9101C-SOT-25; SOT-23-5_HandSoldering
U12: INA219AID; SOIC-8_3.9x4.9mm_P1.27mm_LargePads; MPN INA219AIDCNR; Digi-Key_PN 296-23770-1-ND
U13: PCF8593; SOIC-8_3.9x4.9mm_P1.27mm_LargePads
U14: TPS22917; SOT-23-6_Handsoldering
U20: BQ21040DBVT; SOT-23-6_Handsoldering
U?1: TMP100; SOT-23-6_Handsoldering

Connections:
+3V3_A: C1.1, C2.1, C15.2, C16.2, C22.1, C24.2, J14.1, J14.3, J14.5, J14.7, J18.9, J18.10, U1.4 (~SHDN), U1.6 (VDD), U4.8 (VDD), U6.8 (VDD), U12.5 (VS), U13.3 (~RESET), U13.8 (VDD), U14.6 (VOUT), U?1.3 (ADR1), U?1.4 (VCC), U?1.5 (ADR0)
+3V3_U: C14.1, R12.1, U10.3 (OUT), U14.1 (VIN)
+BATT: C23.2, Q5.2 (S), R18.2, R20.1, R22.2
/Power/BATT+: C20.1, J9.2, Q4.2 (S), Q5.3 (D), R3.2
/Power/BATT-UNPROT: C20.2, J9.1, Q3.3 (S), U11.1 (VM), U11.3 (VSS)
/Power/BATT_CHARGE_PRE_POLARITY: Q4.3 (D), U20.2 (OUT)
BATT_VOLTAGE: R20.2, R21.1, U6.4 (VIN1)
CHARGE_VOLTAGE: J18.11, J18.12, U6.5 (VIN3)
DYNAMO_AC: J7.1, J18.3, J18.4
DYNAMO_POLE_SIG: J18.7, J18.8, R29.1, U13.1 (OSCI)
DYNAMO_SW_1_P: J18.5, U4.1 (IO0)
DYNAMO_SW_2_P: J18.6, U4.2 (IO1)
GNDA: C1.2, C16.1, C21.2, NT1.2, U1.2 (GND), U1.3 (GND), U1.5 (GND), U6.7 (GND)
GND_A: C2.2, C3.2, C14.2, C15.1, C17.2, C18.1, C22.2, C24.1, J14.9, J14.10, J14.11, J14.12, J14.14, J18.15, J18.16, NT1.1, Q3.1 (S), Q4.1 (G), Q5.1 (G), R4.2, R13.2, R19.2, R21.2, R29.2, U4.4 (VSS), U10.5 (GND), U10.6 (GND), U10.7 (GND), U10.8 (GND), U12.6 (GND), U13.4 (GND), U14.2 (GND), U20.5 (GND), U?1.2 (GND)
I2C1_SCL_A: J14.16, U4.6 (SCL), U6.1 (SCL), U12.4 (SCL), U13.6 (SCL), U?1.1 (SCL)
I2C1_SDA_A: J14.15, U4.7 (SDA), U6.2 (SDA), U12.1 (A1), U12.2 (A0), U12.3 (SDA), U13.5 (SDA), U?1.6 (SDA)
unnamed: C21.1, R25.1
unnamed: J7.2, J18.1, J18.2
unnamed: Q3.4 (G), U11.4 (DO)
unnamed: Q3.6 (G), U11.5 (CO)
unnamed: R3.1, U11.2 (VDD)
unnamed: R12.2, R13.1, U10.4 (ADJ)
unnamed: R18.1, U12.8 (IN+)
unnamed: R19.1, U20.4 (ISET)
unnamed: R23.2, U12.7 (IN-)
unnamed: R25.2, U1.1 (OUT), U6.6 (VIN4/VREF)
VCC_A: C3.1, C23.1, J14.2, J14.4, J14.6, J14.8, R22.1, R23.1, U10.1 (EN), U10.2 (IN)
VDYN: C17.1, C18.2, J18.13, J18.14, U20.6 (VIN)
WAKE_A: J14.13, R4.1, U14.3 (ON)
~BATT_CHARGING: U4.3 (IO2), U20.3 (~CHG)

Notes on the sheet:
Addr: 1000001
Addr: 0101000
Connected Internally
Address: 1001010
Address: 1010001
Address: 1001110

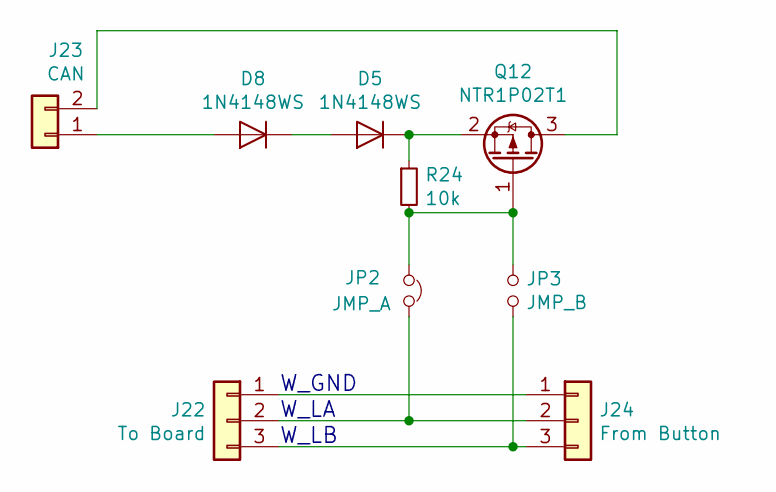
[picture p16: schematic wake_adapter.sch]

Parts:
D5, D8: 1N4148WS; D_SOD-323_HandSoldering
J22: To Board; PinHeader_1x03_P2.54mm_Vertical
J23: CAN; PinHeader_1x02_P2.54mm_Vertical
J24: From Button; JST_XH_B03B-XH-A_03x2.50mm_Straight_LargePads
JP2: JMP_A; SolderJumper-2_P1.3mm_Bridged_Pad1.0x1.5mm
JP3: JMP_B; SolderJumper-2_P1.3mm_Open_Pad1.0x1.5mm
Q12: NTR1P02T1; SOT-23_LargePads
R24: 10k; 0805_Milling

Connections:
unnamed: D5.1 (K), Q12.2 (S), R24.1
unnamed: D5.2 (A), D8.1 (K)
unnamed: D8.2 (A), J23.1
unnamed: J22.1, J24.1
unnamed: J22.2, J24.2, JP2.2
unnamed: J22.3, J24.3, JP3.2
unnamed: J23.2, Q12.3 (D)
unnamed: JP2.1, JP3.1, Q12.1 (G), R24.2

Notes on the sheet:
W_GND
W_LA
W_LB

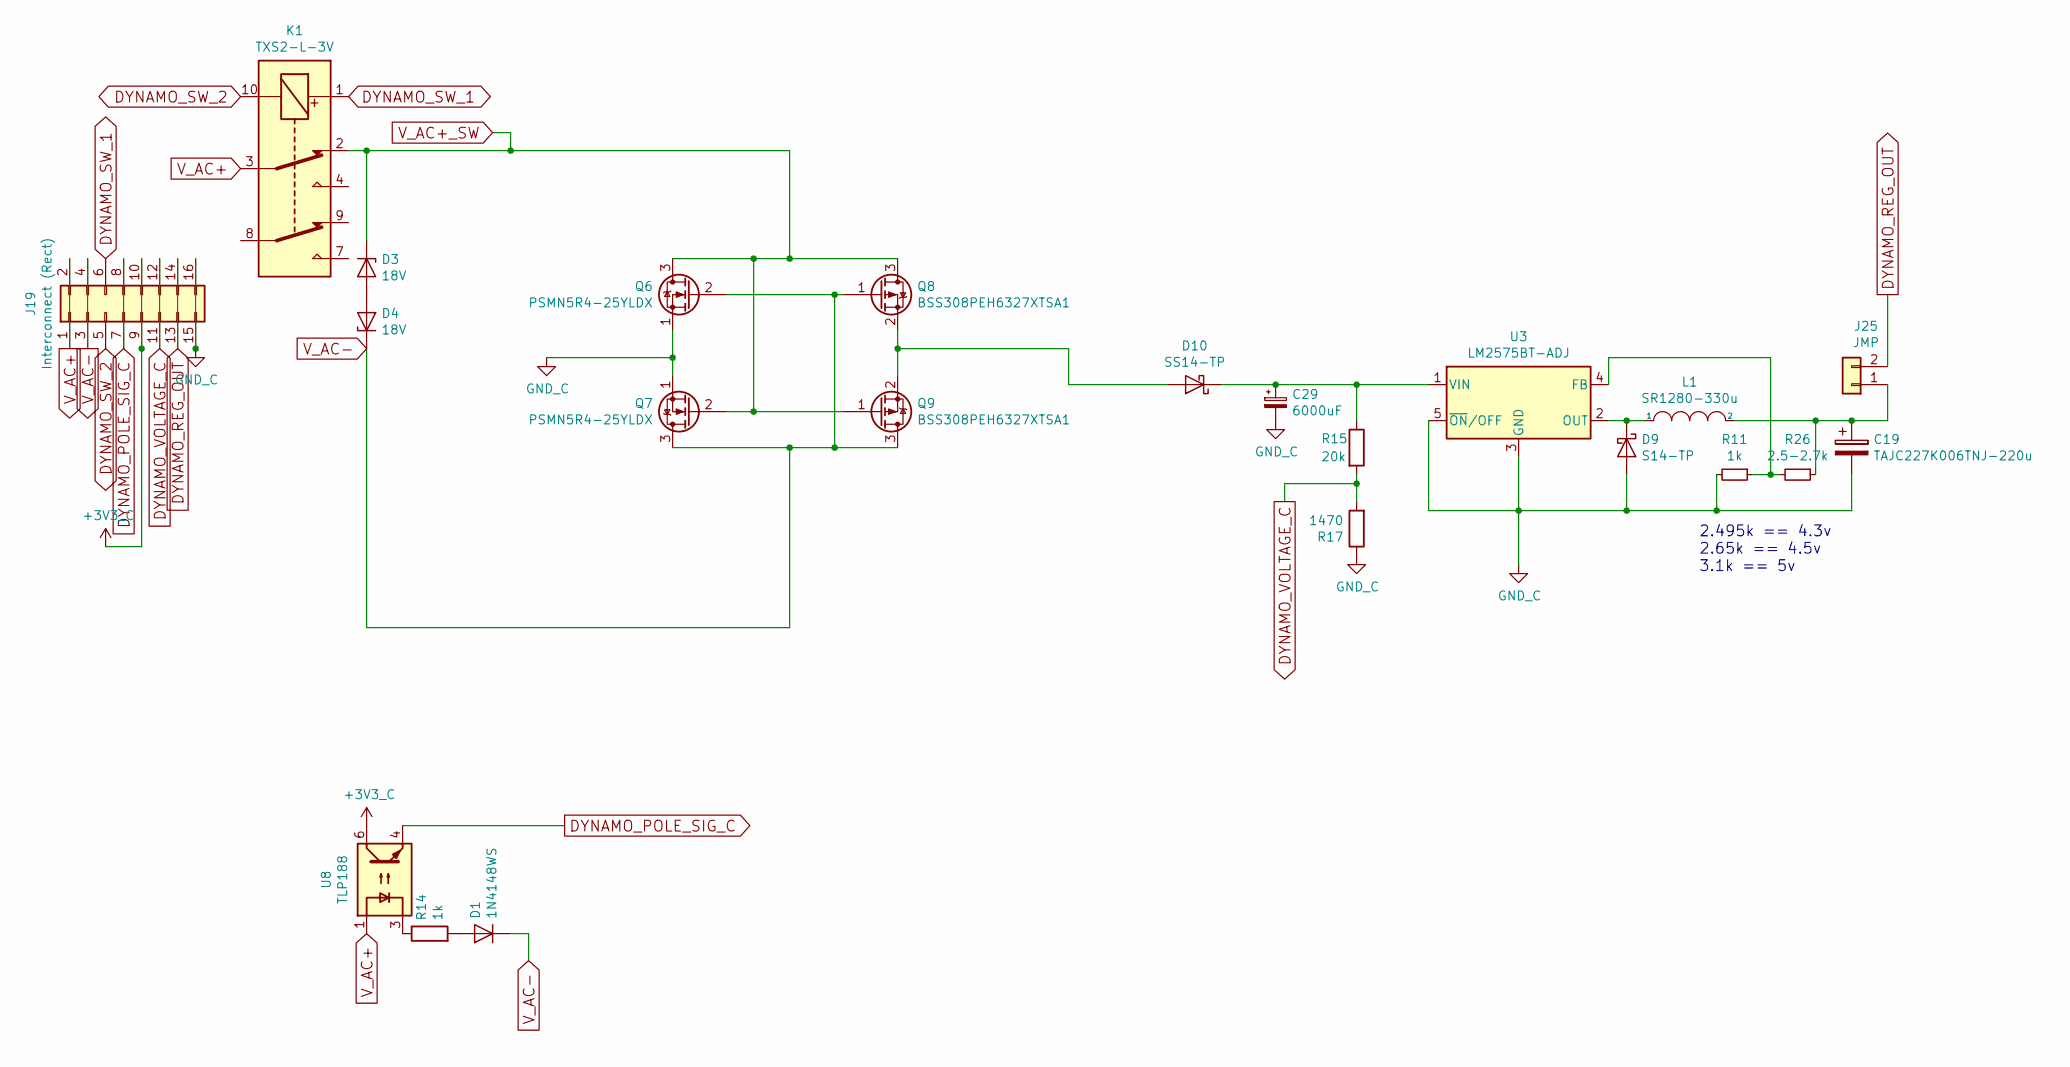
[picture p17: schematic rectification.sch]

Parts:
C19: TAJC227K006TNJ-220u; CP_Tantalum_Case-C_EIA-6032-28_Milling
C29: 6000uF; JST_XH_B02B-XH-A_02x2.50mm_Straight_LargePads
D1: 1N4148WS; D_SOD-323_HandSoldering
D3, D4: 18V; D_DO-201AE_P15.24mm_Horizontal
D9: S14-TP; DO-214AC
D10: SS14-TP; DO-214AC
J19: Interconnect (Rect); PinHeader_2x08_P2.54mm_Vertical_LargePads
J25: JMP; PinHeader_1x02_P2.54mm_Vertical
K1: TXS2-L-3V; Panasonic_TX-S_DPDT
L1: SR1280-330u; SRF1280-PARALLEL
Q6, Q7: PSMN5R4-25YLDX; PSMN5R4-25YLD
Q8, Q9: BSS308PEH6327XTSA1; SOT-23_LargePads
R11, R14: 1k; 0805_Milling
R15: 20k; 0805_Milling
R17: 1470; 0805_Milling
R26: 2.5-2.7k; 0805_Milling
U3: LM2575BT-ADJ; TO-263-5_TabPin3
U8: TLP188; SO-4_Optocoupler_Milling

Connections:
+3V3_C: J19.9, J19.10, U8.6
DYNAMO_POLE_SIG_C: J19.7, J19.8, U8.4
DYNAMO_REG_OUT: J19.13, J19.14, J25.2
DYNAMO_SW_1: J19.6, K1.1
DYNAMO_SW_2: J19.5, K1.10
DYNAMO_VOLTAGE_C: J19.11, J19.12, R15.2, R17.2
GND_C: C19.2, C29.2, D9.2 (A), J19.15, J19.16, Q6.1 (S), Q7.1 (S), R11.2, R17.1, U3.3 (GND), U3.5 (~ON~/OFF)
unnamed: C19.1, J25.1, L1.2, R26.1
unnamed: C29.1, D10.1 (K), R15.1, U3.1 (VIN)
unnamed: D1.2 (A), R14.2
unnamed: D3.2 (A), D4.2 (A)
unnamed: D9.1 (K), L1.1, U3.2 (OUT)
unnamed: D10.2 (A), Q8.2 (S), Q9.2 (S)
unnamed: R11.1, R26.2, U3.4 (FB)
unnamed: R14.1, U8.3
V_AC+: J19.1, J19.2, K1.3, U8.1
V_AC+_SW: D3.1 (K), K1.2, Q6.3 (D), Q7.2 (G), Q8.3 (D), Q9.1 (G)
V_AC-: D1.1 (K), D4.1 (K), J19.3, J19.4, Q6.2 (G), Q7.3 (D), Q8.1 (G), Q9.3 (D)

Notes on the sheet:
2.495k == 4.3v 2.65k == 4.5v 3.1k == 5v

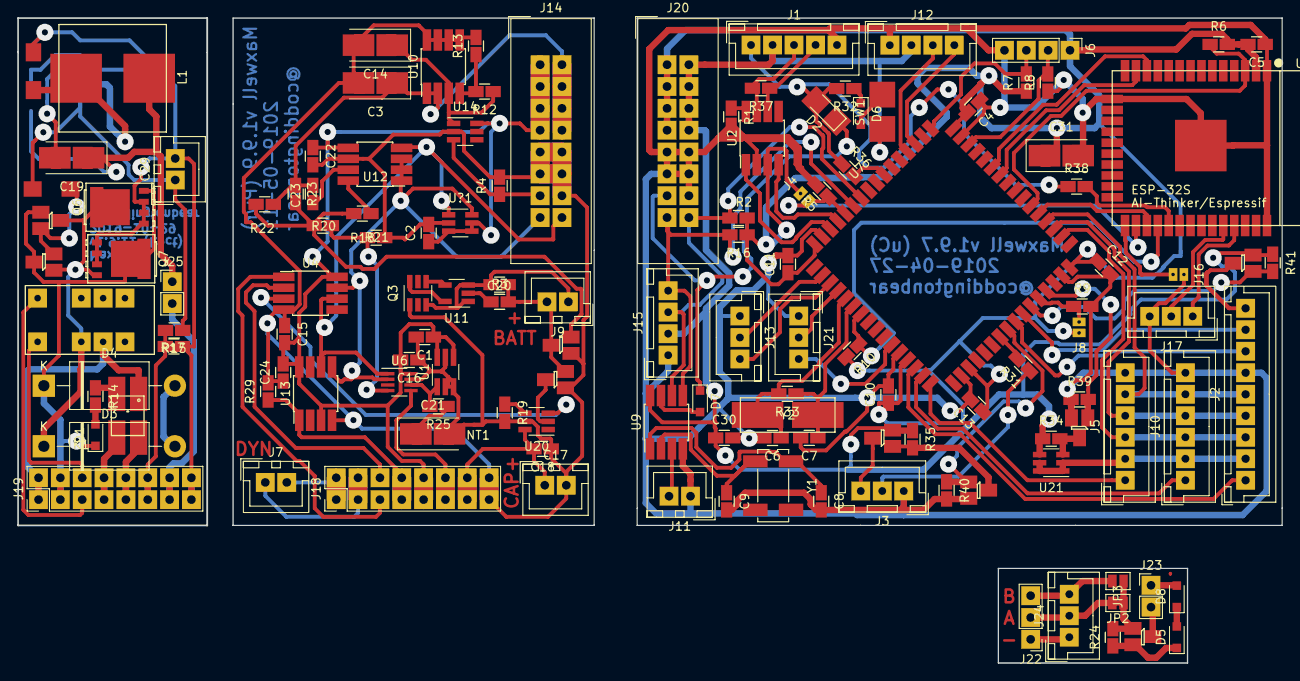
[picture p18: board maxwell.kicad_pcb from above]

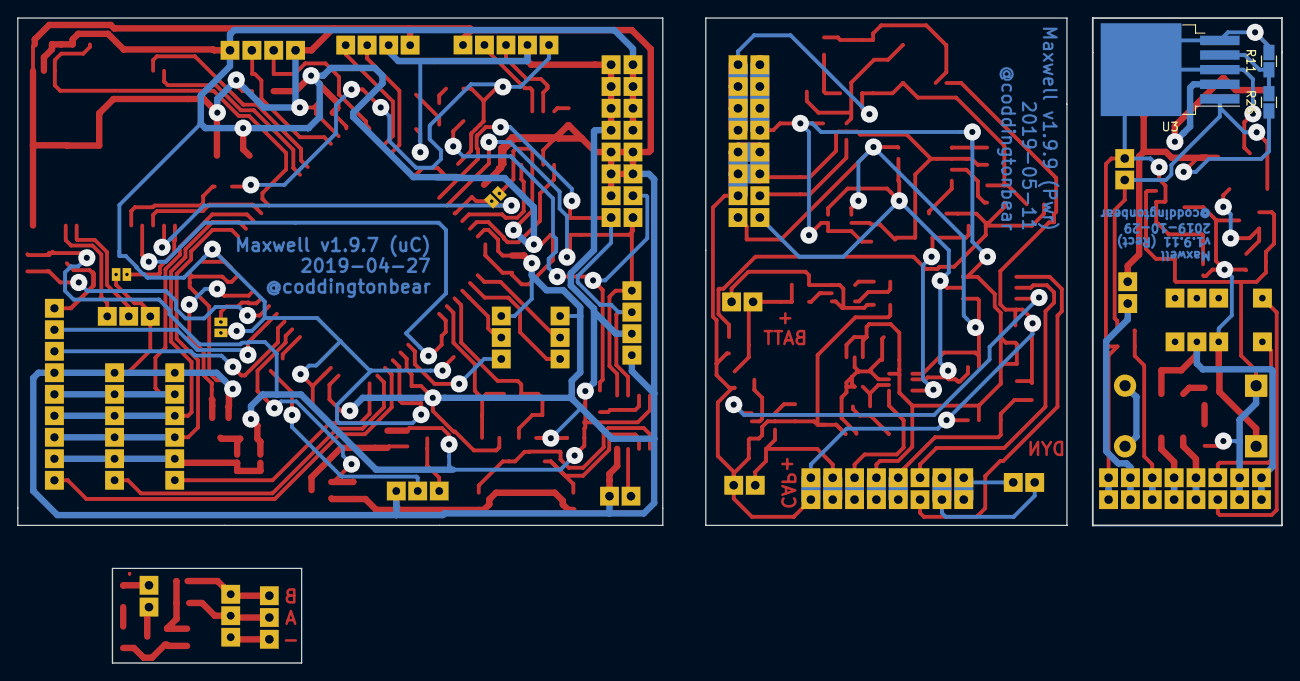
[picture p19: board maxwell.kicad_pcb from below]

Board: 2 copper layers, 147.0 x 75.0 mm, 137 parts (3 on the bottom side), 114 nets.

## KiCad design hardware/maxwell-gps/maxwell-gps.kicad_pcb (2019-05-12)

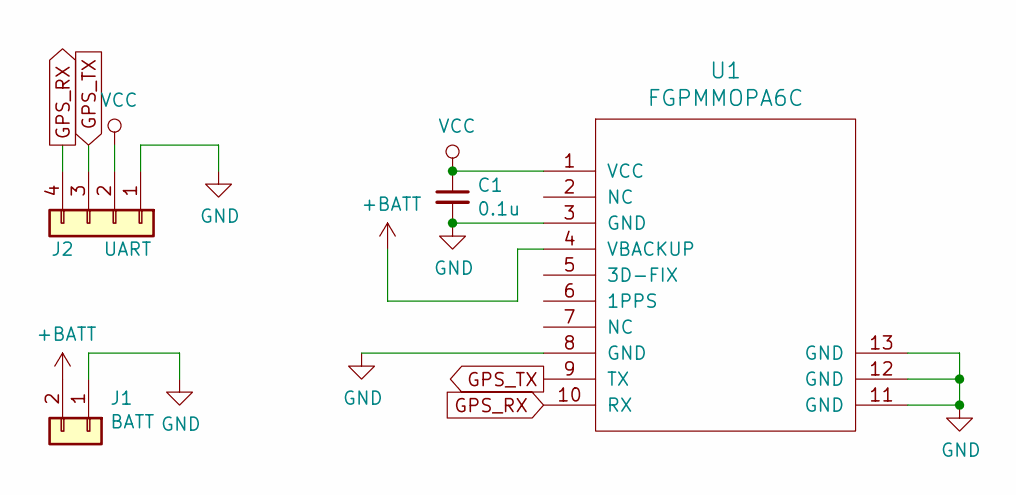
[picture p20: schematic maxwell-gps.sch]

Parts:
C1: 0.1u; 0805_Milling
J1: BATT; JST_XH_B02B-XH-A_02x2.50mm_Straight_LargePads
J2: UART; JST_XH_B04B-XH-A_04x2.50mm_Straight_LargePads
U1: FGPMMOPA6C

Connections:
+BATT: J1.2, U1.4 (VBACKUP)
GND: C1.2, J1.1, J2.1, U1.3 (GND), U1.8 (GND), U1.11 (GND), U1.12 (GND), U1.13 (GND)
GPS_RX: J2.4, U1.10 (RX)
GPS_TX: J2.3, U1.9 (TX)
VCC: C1.1, J2.2, U1.1 (VCC)

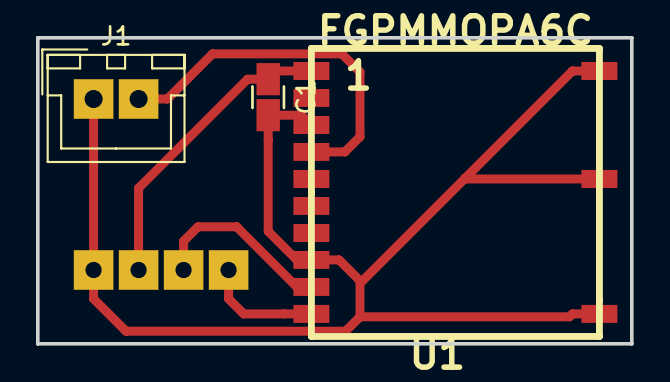
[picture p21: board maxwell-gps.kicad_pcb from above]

Board: 2 copper layers, 33.0 x 17.0 mm, 4 parts (1 on the bottom side), 5 nets.

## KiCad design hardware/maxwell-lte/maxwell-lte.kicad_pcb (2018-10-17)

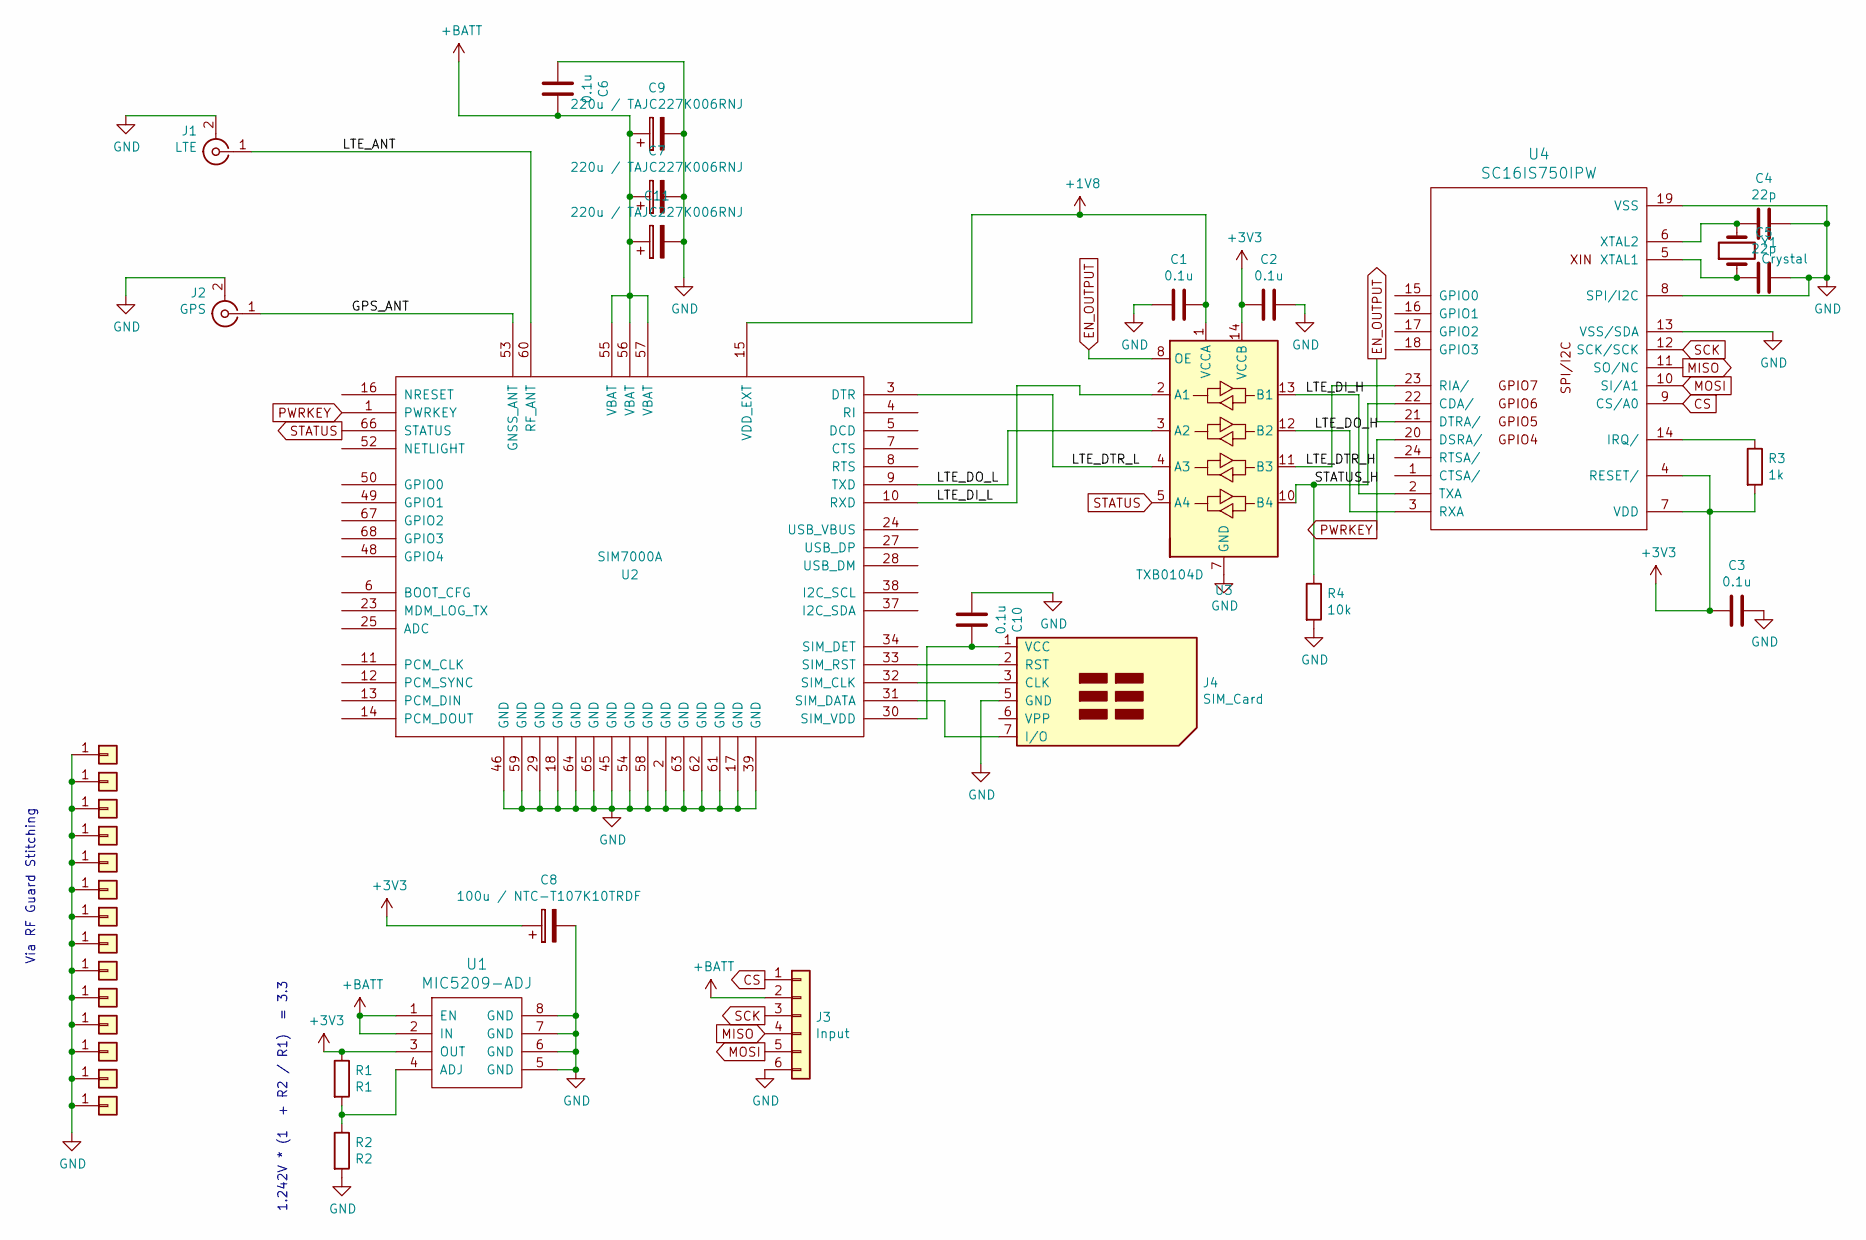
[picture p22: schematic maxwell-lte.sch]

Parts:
C1, C2, C3, C6, C10: 0.1u; 0805_Milling
C4, C5: 22p; 0805_Milling
C7, C9, C11: 220u / TAJC227K006RNJ; CP_Tantalum_Case-C_EIA-6032-28_Milling
C8: 100u / NTC-T107K10TRDF; CP_Tantalum_Case-D_EIA-7343-31_Milling
J1: LTE; SMA_Amphenol_132134_Vertical_Largepads
J2: GPS; SMA_Amphenol_132134_Vertical_Largepads
J3: Input; JST_XH_B06B-XH-A_06x2.50mm_Straight_LargePads
J4: SIM_Card; 78800-0001
J5, J6, J7, J8, J9, J10, J11, J12, J13: Stitching; Thermal_Relief_Via_Milling
R1: R1; 0805_Milling
R2: R2; 0805_Milling
R3: 1k; 0805_Milling
R4: 10k; 0805_Milling
U1: MIC5209-ADJ; SOIC-8_3.9x4.9mm_P1.27mm_LargePads
U2: SIM7000A; SIM7000
U3: TXB0104D; SOIC-14_3.9x8.7mm_P1.27mm_LargePads
U4: SC16IS750IPW; TSSOP-24_4.4x7.8mm_P0.65mm_LargePads
Y1: Crystal; Crystal_HC49-U_Vertical_LargePads

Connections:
+1V8: C1.1, U2.15 (VDD_EXT), U3.1 (VCCA)
+3V3: C2.1, C3.1, C8.1, R1.1, R3.2, U1.3 (OUT), U3.14 (VCCB), U4.4 (RESET/), U4.7 (VDD)
+BATT: C6.1, C7.1, C9.1, C11.1, J3.2, U1.1 (EN), U1.2 (IN), U2.55 (VBAT), U2.56 (VBAT), U2.57 (VBAT)
/GPS_ANT: J2.1 (In), U2.53 (GNSS_ANT)
/LTE_ANT: J1.1 (In), U2.60 (RF_ANT)
/LTE_DI_H: U3.13 (B1), U4.2 (TXA)
/LTE_DI_L: U2.10 (RXD), U3.2 (A1)
/LTE_DO_H: U3.12 (B2), U4.3 (RXA)
/LTE_DO_L: U2.9 (TXD), U3.3 (A2)
/LTE_DTR_H: U3.11 (B3), U4.23 (RIA/)
/LTE_DTR_L: U2.3 (DTR), U3.4 (A3)
/STATUS_H: R4.1, U3.10 (B4), U4.22 (CDA/)
CS: J3.1, U4.9 (CS/A0)
EN_OUTPUT: U3.8 (OE), U4.21 (DTRA/)
GND: C1.2, C2.2, C3.2, C4.2, C5.2, C6.2, C7.2, C8.2, C9.2, C10.2, C11.2, J1.2 (Ext), J2.2 (Ext), J3.6, J4.5 (GND), J5.1, J6.1, J7.1, J8.1, J9.1, J10.1, J11.1, J12.1, J13.1, R2.2, R4.2, U1.5 (GND), U1.6 (GND), U1.7 (GND), U1.8 (GND), U2.2 (GND), U2.17 (GND), U2.18 (GND), U2.29 (GND), U2.39 (GND), U2.45 (GND), U2.46 (GND), U2.54 (GND), U2.58 (GND), U2.59 (GND), U2.61 (GND), U2.62 (GND), U2.63 (GND), U2.64 (GND), U2.65 (GND), U3.7 (GND), U4.8 (SPI/I2C), U4.13 (VSS/SDA), U4.19 (VSS); also elsewhere on the board
MISO: J3.4, U4.11 (SO/NC)
MOSI: J3.5, U4.10 (SI/A1)
unnamed: C4.1, U4.6 (XTAL2), Y1.2
unnamed: C5.1, U4.5 (XTAL1), Y1.1
unnamed: C10.1, J4.1 (VCC), U2.30 (SIM_VDD)
unnamed: J4.2 (RST), U2.33 (SIM_RST)
unnamed: J4.3 (CLK), U2.32 (SIM_CLK)
unnamed: J4.7 (I/O), U2.31 (SIM_DATA)
unnamed: R1.2, R2.1, U1.4 (ADJ)
unnamed: R3.1, U4.14 (IRQ/)
PWRKEY: U2.1 (PWRKEY), U4.20 (DSRA/)
SCK: J3.3, U4.12 (SCK/SCK)
STATUS: U2.66 (STATUS), U3.5 (A4)

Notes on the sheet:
1.242V * (1 + R2 / R1) = 3.3
Via RF Guard Stitching

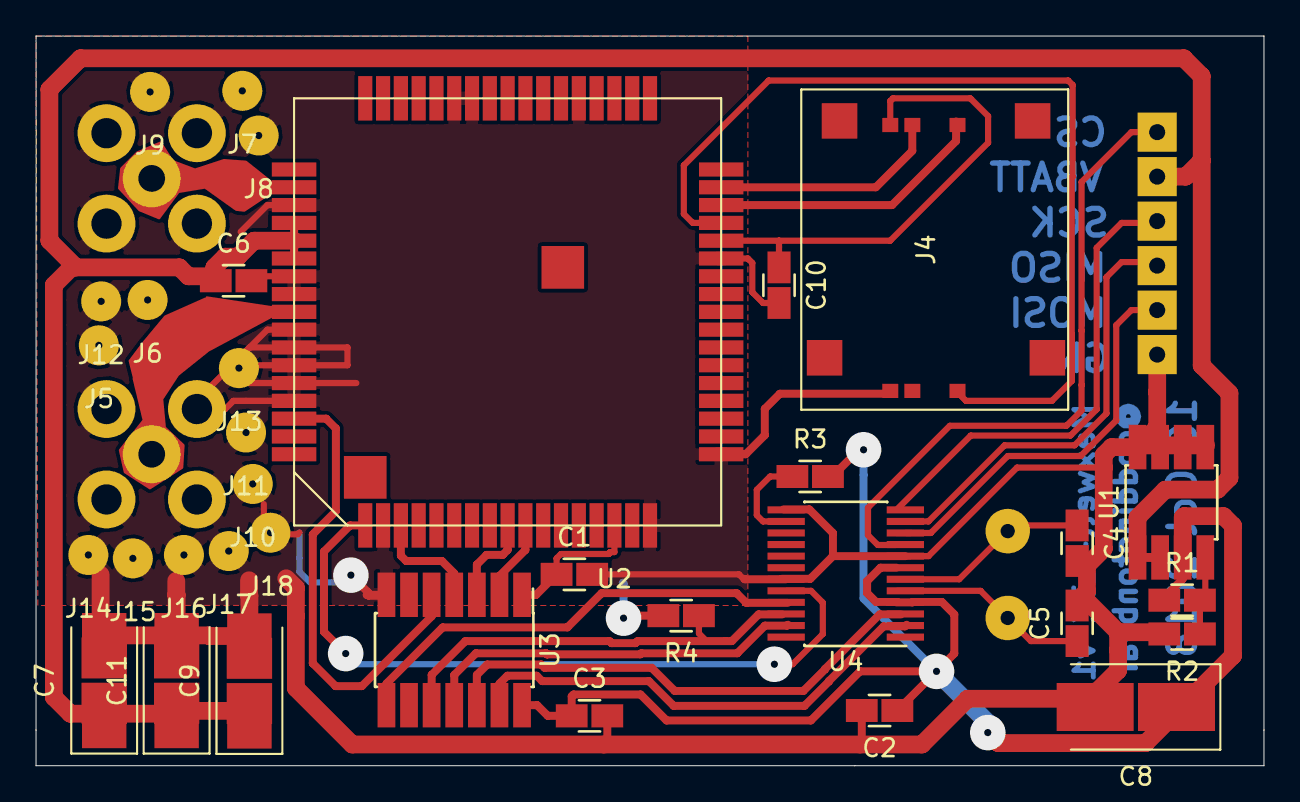
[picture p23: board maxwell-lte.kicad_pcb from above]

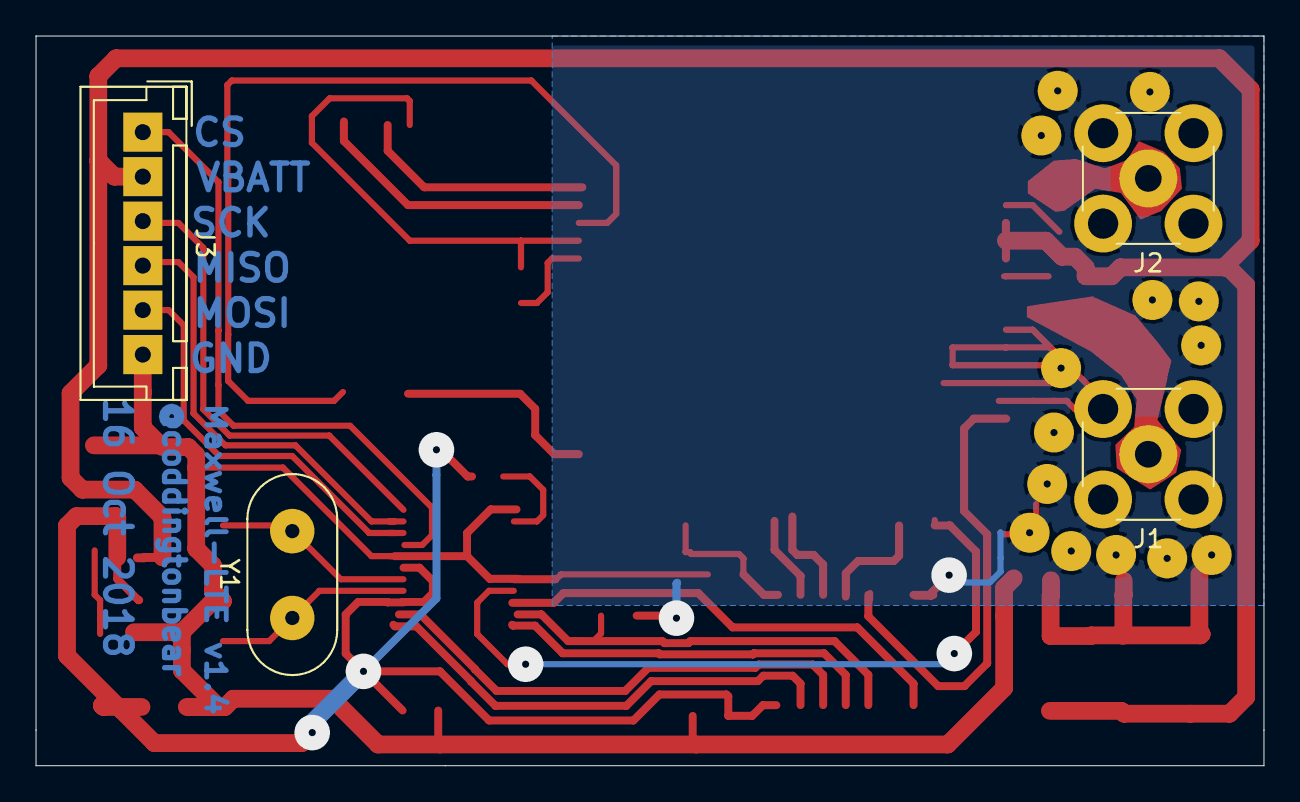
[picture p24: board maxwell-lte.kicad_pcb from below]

Board: 2 copper layers, 69.0 x 41.0 mm, 38 parts (4 on the bottom side), 28 nets.

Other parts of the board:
J14: Stiching; Thermal_Relief_Via_Milling
J15, J16, J17, J18: Stitching; Thermal_Relief_Via_Milling

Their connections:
GND: J14.1, J15.1, J16.1, J17.1, J18.1; also elsewhere on the board

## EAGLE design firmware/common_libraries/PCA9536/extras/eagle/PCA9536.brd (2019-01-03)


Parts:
R-RGB-BLUE: (1K/0.5W, 1%, ERJ-P06F1001V); 0805
R-RGB-GREEN: (1K/0.5W, 1%, ERJ-P06F1001V); 0805
R-RGB-RED: (1K/0.5W, 1%, ERJ-P06F1001V); 0805
RGB-D-LED: (GREEN, HSMG-C170); DIODE_0805
RGB-D-RGB: (RGB, HSMF-C118); DIODE_LED_1210_RGB
RGB-J1: RGB-HEADER-8-PIN; HEADER_2.54MM_8_PIN_VER
RGB-PCA9536: PCA9536D; SOIC-8-NARROW
RGB-PCA9536-C-BY: (100nF/50V, X7R, 5%, 08055C104J4Z2A); 0805
RGB-PCA9536-R-SCL, RGB-PCA9536-R-SDA: (2K2/0.25W, 5%, ERJ-T06J222V); 0805
RGB-R-LED: (1K/0.5W, 1%, ERJ-P06F1001V); 0805

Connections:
RGB-GND: RGB-D-LED.C, RGB-J1.5, RGB-PCA9536.4 (GND), RGB-PCA9536-C-BY.1 (A)
RGB-IO-0: R-RGB-BLUE.1, RGB-J1.8, RGB-PCA9536.1 (I/O0)
RGB-IO-1: R-RGB-GREEN.1, RGB-J1.7, RGB-PCA9536.2 (I/O1)
RGB-IO-2: R-RGB-RED.1, RGB-J1.6, RGB-PCA9536.3 (I/O2)
RGB-IO-3: RGB-J1.4, RGB-PCA9536.5 (I/O3)
RGB-POWER: RGB-D-LED.A, RGB-R-LED.1
RGB-R-BLUE: R-RGB-BLUE.2, RGB-D-RGB.4
RGB-R-GREEN: R-RGB-GREEN.2, RGB-D-RGB.3
RGB-R-RED: R-RGB-RED.2, RGB-D-RGB.2
RGB-SCL: RGB-J1.3, RGB-PCA9536.6 (SCL), RGB-PCA9536-R-SCL.1
RGB-SDA: RGB-J1.2, RGB-PCA9536.7 (SDA), RGB-PCA9536-R-SDA.1
RGB-VCC: RGB-D-RGB.1, RGB-J1.1, RGB-PCA9536.8 (VCC), RGB-PCA9536-C-BY.2 (C), RGB-PCA9536-R-SCL.2, RGB-PCA9536-R-SDA.2, RGB-R-LED.2

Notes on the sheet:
RGB LED MODULE + I2C EXPANDER
(I2C ADDRESS: 0x41 / 65)



Board: 2 copper layers, 15.2 x 15.2 mm, 11 parts (6 on the bottom side), 12 nets.

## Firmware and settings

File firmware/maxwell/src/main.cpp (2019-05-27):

#include "main.h"
#include <Arduino.h>
#undef min
#undef max
#include <libmaple/iwdg.h>
#include <SdFat.h>
#include <SPI.h>
#include <Wire.h>
#include <ArduinoJson.h>
#include <SC16IS750.h>
#include <multiserial.h>

#include "multiserial.h"
#include "power.h"
#include "neopixel.h"
#include "serial_commands.h"
#include "power.h"
#include "pin_map.h"
#include "main.h"
#include "lte.h"
#include "status.h"
#include "tasks.h"
#include "bluetooth.h"
#include "util.h"
#include "display.h"

SC16IS750 LTEUart = SC16IS750(
    PIN_SPI_CS_B,
    SC16IS750_CHAN_A,
    14745600UL
);

MultiSerial Output;

HashMap<String, double> Statistics;

SdFat filesystem(&SPI);

Logger Log(&filesystem);

HardwareSerial GPSUart = UART4;

void setup() {
    power::setWake(true);

    afio_cfg_debug_ports(AFIO_DEBUG_SW_ONLY);
    iwdg_init(IWDG_PRE_256, 4095);

    Output.addInterface(&BTSerial);
    Output.begin(230400, SERIAL_8E1);
    Output.println("[Maxwell 2.0]");
    Output.flush();

    Wire.begin();
    power::init();

    digitalWrite(PIN_SPI_CS_A, HIGH);
    digitalWrite(PIN_SPI_CS_B, HIGH);
    digitalWrite(DISPLAY_CS, HIGH);
    pinMode(PIN_SPI_CS_A, OUTPUT);
    pinMode(PIN_SPI_CS_B, OUTPUT);
    pinMode(DISPLAY_CS, OUTPUT);

    SPI.setModule(2);
    SPI.begin();

    if(!filesystem.begin(PIN_SPI_CS_A, SD_SCK_MHZ(100))) {
        filesystem.initErrorPrint(&Output);
        Display.addAlert("Log init failed");
    } else {
        Log.begin();
    }

    Log.log(String("Device reset: ") + String(RCC_BASE->CSR, HEX));
    Output.print("Device reset: ");
    if(RCC_BASE->CSR & (1 << 31)) {
        Log.log("Reset reason: Low Power");
        Output.println("Low Power");
    }
    if(RCC_BASE->CSR & (1 << 30)) {
        Log.log("Reset reason: Window Watchdog");
        Output.println("Window Wathdog");
    }
    if(RCC_BASE->CSR & (1 << 29)) {
        Log.log("Reset reason: Independent Watchdog");
        Output.println("Independent Wathdog");
    }
    if(RCC_BASE->CSR & (1 << 28)) {
        Log.log("Reset reason: Software Reset");
        Output.println("Software Reset");
    }
    if(RCC_BASE->CSR & (1 << 27)) {
        Log.log("Reset reason: POR/PDR");
        Output.println("POR/PDR");
    }
    if(RCC_BASE->CSR & (1 << 26)) {
        Log.log("Reset reason: NRST");
        Output.println("NRST");
    }
    if(RCC_BASE->CSR & (1 << 25)) {
        Log.log("Reset reason: BOR");
        Output.println("BOR");
    }
    // Clear reset flags
    RCC_BASE->CSR |= RCC_CSR_RMVF;

    digitalWrite(PIN_BT_KEY, LOW);
    pinMode(PIN_BT_KEY, OUTPUT);
    digitalWrite(PIN_BT_DISABLE_, HIGH);
    pinMode(PIN_BT_DISABLE_, OUTPUT);

    delay(100);

    Display.begin();
    Display.setContrast(180);

    // power::init() is earlier
    bluetooth::init();
    tasks::init();
    neopixel::init();
    console::init();
    status::init();
    display::init();

    LTEUart.setSpiBus(&SPI);
    LTEUart.begin(115200, true);
    if(!LTEUart.ping()) {
        Output.println("Error connecting to UART over SPI; no LTE available.");
        Display.addAlert("LTE init failed");
    } else {
        LTEUart.GPIOSetPinMode(PIN_LTE_DTR, OUTPUT);
        LTEUart.GPIOSetPinMode(PIN_LTE_OE, OUTPUT);
        LTEUart.GPIOSetPinState(PIN_LTE_DTR, LOW);
        LTEUart.GPIOSetPinState(PIN_LTE_OE, HIGH);
        lte::asyncEnable();
    }

    console::prompt();

    Output.println("Ready.");
    Output.flush();
    Log.log("Ready");
}

void loop() {
    loopModules();

    console::loop();
}

void loopModules() {
    iwdg_feed();

    tasks::loop();
}

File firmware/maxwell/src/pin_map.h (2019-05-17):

#pragma once

#include <PCA9536.h>

#define PIN_BT_DISABLE_ PC7
#define PIN_BT_KEY PC6

#define PIN_SPI_CS_A PA2
#define PIN_SPI_CS_B PA1

#define PIN_NEOPIXEL PA7
#define PIN_ENABLE_NEOPIXEL PC4
#define PIN_ENABLE_AUX PB10

#define DISPLAY_BACKLIGHT_ON_ PB1
#define DISPLAY_CS PA0
#define DISPLAY_DC PC5
#define DISPLAY_RST PB0

#define PIN_POWER_ON PB3

#define BUTTON_LEFT_A PC13
#define BUTTON_LEFT_B PC14
#define BUTTON_RIGHT_A PC15
#define BUTTON_RIGHT_B PC3

// EXTERNAL: LTE Module
#define PIN_LTE_DTR 7
#define PIN_LTE_STATUS 6
#define PIN_LTE_OE 5
#define PIN_LTE_PWRKEY 4

// EXTERNAL: Power/ADC
#define PIN_ADC_BATT_VOLTAGE 1
#define PIN_ADC_DYNAMO_VOLTAGE 2

// EXTERNAL: Power/IO
#define PIN_RECTIFIER_RELAY_A IO0
#define PIN_RECTIFIER_RELAY_B IO1
#define PIN_PWR_I_BATT_CHARGING IO2

#define BTSerial Serial
#define UART2 Serial1
#define UART3 Serial2
#define UART4 Serial3
#define UART5 Serial4

#define I2C_SCL PB6
#define I2C_SDA PB7

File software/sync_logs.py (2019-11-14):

import argparse
import binascii
import contextlib
import datetime
import logging
import os
import sys
import time

import serial
from typing import Iterable, List


logger = logging.getLogger(__name__)


def send_command(connection, cmd, *args):
    full_command = ' '.join([
        cmd,
        *(str(arg) for arg in args)
    ])
    connection.write(full_command.encode('utf-8'))
    connection.write(b'\n')

    logger.debug("Sending command: %s", full_command)

    # Consume the echo'd back command
    connection.readline()


def get_response_for_command(connection, cmd, *args) -> Iterable[str]:
    send_command(connection, cmd, *args)

    while True:
        line = connection.readline()
        if(not line.strip()):
            break

        if line.decode('utf-8').strip().startswith('>>'):
            return

        yield line.decode('utf-8').rstrip()


@contextlib.contextmanager
def timeout(connection, timeout):
    original_timeout = connection.timeout
    connection.timeout = timeout

    yield

    connection.timeout = original_timeout


def get_verified_response_for_command(
    connection,
    cmd,
    *args,
    max_attempts=10
) -> Iterable[str]:
    last = []

    attempts = 0

    while attempts < max_attempts:
        current = list(get_response_for_command(connection, cmd, *args))

        if current == last:
            for line in current:
                yield line

            return

        last = current
        attempts += 1

    raise ValueError("Failed to get verified response")


def list_logs(connection) -> List[str]:
    indentations = {}
    logs = []

    for line in get_response_for_command(
        connection,
        'log_list',
    ):
        indentation_level = len(line) - len(line.lstrip())
        indentations[indentation_level] = line.strip()

        if not line.endswith('.log'):
            continue

        logs.append(
            ''.join([
                v for k, v in sorted(
                    indentations.items(), key=lambda row: row[0]
                )
            ])
        )

    return logs


def get_log(connection, path) -> Iterable[str]:
    send_command(
        connection,
        'log_print_chk',
        path
    )
    started = time.time()
    line_count = 0
    error_count = 0
    byte_count = 0
    while True:
        line = connection.readline()
        line_count += 1
        if not line.strip():
            break

        if line.decode('utf-8').strip().startswith('>>'):
            return

        try:
            data, checksum = line.split(b'\t::::\t')
        except ValueError:
            # We probably lost a character in our delimiter
            connection.write(b'0')
            error_count += 1
            continue

        if binascii.crc32(data) == int(checksum):
            connection.write(b'1')
        else:
            connection.write(b'0')
            error_count += 1

        byte_count += len(data) + 1

        yield data.decode('utf-8').strip()

    logger.info(
        'Successfully received (%.1f%% error; %.1fkB at %.3fkBps)',
        error_count / line_count * 100,
        (byte_count / 1000),
        (byte_count / 1000) / (time.time() - started)
    )


def log_checksum(connection, filename) -> int:
    with timeout(connection, 60):
        lines = ' '.join(get_verified_response_for_command(
            connection,
            'log_crc32',
            filename,
        ))
        if 'Error' in lines:
            return 0
        return int(lines)


def log_size(connection, filename) -> int:
    lines = ' '.join(get_verified_response_for_command(
        connection,
        'log_size',
        filename,
    ))
    if 'Error' in lines:
        return 0
    return int(lines)


def parse_date(date_str):
    return datetime.datetime.strptime(
        date_str,
        "%Y-%m-%d"
    )


def get_local_file_checksum(filename) -> int:
    with open(filename, 'rb') as inf:
        data = inf.read()

    return binascii.crc32(data)


def main(*args):
    parser = argparse.ArgumentParser()
    parser.add_argument('port')
    parser.add_argument('destination')
    parser.add_argument('--log-level', default='INFO')
    parser.add_argument('--date', type=parse_date)
    args = parser.parse_args()

    logging.basicConfig(
        level=logging.getLevelName(args.log_level)
    )

    connection = serial.Serial(args.port, baudrate=115200, timeout=0.25)

    logs = list(list_logs(connection))
    for filename in logs:
        logger.info('Filename: %s', filename)

        try:
            filename_date = datetime.datetime.strptime(
                filename,
                "%Y/%m/%d/%H%M%S.log"
            )
        except ValueError:
            logger.warning("Unable to parse date.")
            filename_date = datetime.datetime(1970, 1, 1)

        if (
            args.date and
            (
                filename_date < args.date or
                filename_date > args.date + datetime.timedelta(days=1)
            )
        ):
            logger.info("Skipped; date not in requested range")
            continue

        checksum = log_checksum(connection, filename)
        local_checksum = 0
        local_path = os.path.join(
            args.destination,
            filename
        )

        if os.path.exists(local_path):
            local_checksum = get_local_file_checksum(local_path)

        if local_checksum == checksum:
            logger.info('Already downloaded')
            continue

        logger.info('Downloading...')
        os.makedirs(os.path.dirname(local_path), exist_ok=True)
        with open(local_path, 'w') as outf:
            for line in get_log(connection, filename):
                outf.write(line)
                outf.write('\n')


if __name__ == '__main__':
    main(*sys.argv[1:])

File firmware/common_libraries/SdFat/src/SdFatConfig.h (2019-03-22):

/**
 * Copyright (c) 2011-2018 Bill Greiman
 * This file is part of the SdFat library for SD memory cards.
 *
 * MIT License
 *
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
 * THE SOFTWARE IS PROVIDED "AS IS", WITHOUT WARRANTY OF ANY KIND, EXPRESS
 * OR IMPLIED, INCLUDING BUT NOT LIMITED TO THE WARRANTIES OF MERCHANTABILITY,
 * FITNESS FOR A PARTICULAR PURPOSE AND NONINFRINGEMENT. IN NO EVENT SHALL THE
 * AUTHORS OR COPYRIGHT HOLDERS BE LIABLE FOR ANY CLAIM, DAMAGES OR OTHER
 * LIABILITY, WHETHER IN AN ACTION OF CONTRACT, TORT OR OTHERWISE, ARISING
 * FROM, OUT OF OR IN CONNECTION WITH THE SOFTWARE OR THE USE OR OTHER
 * DEALINGS IN THE SOFTWARE.
 */
/**
 * \file
 * \brief configuration definitions
 */
#ifndef SdFatConfig_h
#define SdFatConfig_h
#include <Arduino.h>
#include <stdint.h>
#ifdef __AVR__
#include <avr/io.h>
#endif  // __AVR__
//------------------------------------------------------------------------------
/**
 * Set INCLUDE_SDIOS nonzero to include sdios.h in SdFat.h.
 * sdios.h provides C++ style IO Streams.
 */
#define INCLUDE_SDIOS 0
//------------------------------------------------------------------------------
/**
 * Set USE_LONG_FILE_NAMES nonzero to use long file names (LFN).
 * Long File Name are limited to a maximum length of 255 characters.
 *
 * This implementation allows 7-bit characters in the range
 * 0X20 to 0X7E except the following characters are not allowed:
 *
 *  < (less than)
 *  > (greater than)
 *  : (colon)
 *  " (double quote)
 *  / (forward slash)
 *  \ (backslash)
 *  | (vertical bar or pipe)
 *  ? (question mark)
 *  * (asterisk)
 *
 */
#define USE_LONG_FILE_NAMES 1
//------------------------------------------------------------------------------
/**
 * If the symbol ENABLE_EXTENDED_TRANSFER_CLASS is nonzero, the class SdFatEX
 * will be defined. If the symbol ENABLE_SOFTWARE_SPI_CLASS is also nonzero,
 * the class SdFatSoftSpiEX will be defined.
 *
 * These classes used extended multi-block SD I/O for better performance.
 * the SPI bus may not be shared with other devices in this mode.
 */
#define ENABLE_EXTENDED_TRANSFER_CLASS 0
//------------------------------------------------------------------------------
/**
 * If the symbol USE_STANDARD_SPI_LIBRARY is zero, an optimized custom SPI
 * driver is used if it exists.  If the symbol USE_STANDARD_SPI_LIBRARY is
 * one, the standard Arduino SPI.h library is used with SPI. If the symbol
 * USE_STANDARD_SPI_LIBRARY is two, the SPI port can be selected with the
 * constructors SdFat(SPIClass* spiPort) and SdFatEX(SPIClass* spiPort).
 */
#define USE_STANDARD_SPI_LIBRARY 0
//------------------------------------------------------------------------------
/**
 * If the symbol ENABLE_SOFTWARE_SPI_CLASS is nonzero, the class SdFatSoftSpi
 * will be defined. If ENABLE_EXTENDED_TRANSFER_CLASS is also nonzero,
 * the class SdFatSoftSpiEX will be defined.
 */
#define ENABLE_SOFTWARE_SPI_CLASS 0
//------------------------------------------------------------------------------
/** If the symbol USE_FCNTL_H is nonzero, open flags for access modes O_RDONLY,
 * O_WRONLY, O_RDWR and the open modifiers O_APPEND, O_CREAT, O_EXCL, O_SYNC
 * will be defined by including the system file fcntl.h.
 */
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

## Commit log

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2017-12-03 Update schematic to send +BATT via CAN instead of 3V3.
    [maxwell.sch]
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2017-12-04 Updating schematic to add reverse polarity protection, higher-current diodes for zener limiting, and a low-side n-channel mosfet for enabling/disabling devices receiving direct battery power (limitin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
    [maxwell.kicad_pcb, maxwell.sch, microcontroller.sch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]
2017-12-05 More minor changes and fixes.
    [maxwell.kicad_pcb, maxwell.sch, microcontroller.sch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]
2017-12-06 More fixes, additions, improvements.
    [maxwell.kicad_pcb, maxwell.sch, microcontroller.sch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]
2017-12-08 Fixed just...an unbelievable number of bugs.
    [maxwell.kicad_pcb, maxwell.sch, microcontroller.sch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]
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2017-12-08 Updating the front layer footprint for the QFP44.
    [maxwell.kicad_pcb]
2017-12-08 Setting origin point; excluding gcode files from git.
    [maxwell.kicad_pcb]
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2017-12-09 Move current measurement to battery side of ldo; obviously. Also, remove now-redundant second current sense trace.
    [maxwell.kicad_pcb, microcontroller.sch, power.sch]
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2018-01-22 Fixing canbus settings; display received messages; adding error reporting.
    [main.cpp]
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2018-02-02 Updating maxwell-remote to v2.0; adds a variety of fixes including:
    Layout:
    * Use of incorrect footprint for NDS332 (should be SSOT-3 rathe
    than SOT-23)
    * Inverted default powered states for screen and bluetooth module.
    * Fixed 32kHz crystal footprint.
    * Swapped surface-mount capacitors for through-hole for durability.
    I've torn the surface-mount ones off the board at least twice now;
    they are not likely to survive long in a high-vibration environment.
    * General layout improvements.
    Functional:
    * Linked both UART2 and UART1 to Bluetooth module. Only UART1 can be
    used for programming, but UART1 is _usually_ used for SerialUSB and
    thus should be avoided given that the USB hardwar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
    [maxwell-remote.kicad_pcb, maxwell-remote.sch]
2018-02-03 Updating boardfile to include a little logo, and much bigger pads for everything that'll be exposed to physical strain.
    [maxwell-remote.kicad_pcb]
2018-02-03 Updating PCB to include a few more Cu text indicators; minor layout improvements. Down to just 37 vias.
    [maxwell-remote.kicad_pcb]
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2018-02-17 Updating maxwell-polarity, but I'm not likely to use those changes; instead, let's just fix maxwel.
    [maxwell-polarity.sch, microcontroller.sch, polarity.sch]
2018-02-17 Maxwell Board v2.0;
    Adds:
    * On-board P-MOS polarity protection.
    * Adds On-board GPS (PA6C)
    * Adds On-board WIFI, and BLE (ESP32)
    * Connectors for 2x external UART devices.
    * Connectors for 2x external SPI devices.
    * Connector for I2C devices.
    Removals:
    * Removes on-board GSM; will add later via UART connectors mentioned
    above.
    * Removes on-board boost charging. Can later add this functionality via
    provided connectors.
    Changes:
    * Although the GNDPWR ground reference still exists, only neopixels
    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
    [maxwell.kicad_pcb, maxwell.sch, microcontroller.sch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]
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2018-03-17 Maxwell-remote v3; swapping HC-05 for ESP32 because all of my HC-05s are dead.
    [maxwell-remote.sch]
2018-03-19 Fixing problems on maxwell-remote board; adding I2C pull-up resistors; fixing 8Mhz xtal package (required removing 32khz crystal).
    [maxwell-remote.kicad_pcb, maxwell-remote.sch]
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2018-03-25 Never made the new version of maxwell remote; reverting schematics to v2.0.
    [maxwell-remote.kicad_pcb, maxwell-remote.sch]
2018-03-27 Multitudinous updates:
    * Adding watchdog timer (iwdg) as the sole failsafe method.
    * Updating sleep mode to instead wake every 14s to feed the watchdog,
    then go back to sleep (forever).
    * Swapping speedometer font for Michroma@24pt
    * Adding (semi-broken) functionality allowing the display to be turned
    off.
    * Adding functionality allowing display brightness (per API 'contrast')
    to be adjusted.
    * Adding functionality for receiving charging status over can.
    * Show battery voltage in inverse if charging.
    * Show asterisk post-voltage to indicate a fully-charged battery.
    [display.cpp, display.h, main.cpp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]
2018-03-27 Multitudinous updates (but this time to the base unit):
    * Adding better documentation for can msg formats.
    * Adding watchdog timer as sole failsafe method; like what I did
    for the remote, updating the sleep method to instead wake every
    14s to feed the watchdog, then going to sleep. Forever.
    * Smooth speed reports out by continuously averaging over five
    measurements.
    * Chirp when going to sleep, too.
    * Removing code returning dynamo voltages now that I'm not recording
    that.
    [main.cpp, power.cpp, power.h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]
2018-04-03 Fixing a type problem.
    [main.cpp]
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2018-04-11 Report reset reason at top of log message.
    [main.cpp]
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2018-04-23 Properly disable CanBus Transceiver during sleep; flipping display now that the new hardware design is oriented in the opposite direction.
    [display.cpp, main.cpp, serial_commands.cpp]
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2018-04-23 Don't use std::vector; adding long-press actions; fixing large font.
    [SdFatConfig.h, display.cpp, main.cpp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]
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2018-04-28 Welp; I had accidentally re-used some can msg ids; fixed.
    [main.cpp]
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2018-05-23 Turning off handleEspStatus to see if this is the source of random reboots.
    [main.cpp]
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2018-05-29 Updating to v5.0 of the remote's main PCB.
    [maxwell-remote.kicad_pcb, maxwell-remote.sch]
2018-06-04 Adding new FPC-connected board for extra connectors, can transceiver, voltage regulator.
    [maxwell-remote-2.kicad_pcb, maxwell-remote-2.sch, maxwell-remote.kicad_pcb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]
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2018-07-01 Fixing footprint for MOSFET packages; enable/disable VBATT instead of GND for screen.
    [maxwell-remote-2.kicad_pcb, maxwell-remote-2.sch]
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2018-09-17 Updating to include possible GPIOs for PPS and 3DFIX.
    [maxwell-remote-gps.kicad_pcb, maxwell-remote-gps.sch]
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2018-10-02 Updating UART settings to work properly; apparently, if you run the UART too slowly, GPIOs won't work; increasing to 2MHz fixed it.
    [SC16IS750.cpp, main.cpp, serial_commands.cpp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]
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2018-10-14 Increasing minimum track width from 0.25 to 0.35 to make traces a little more resilient.
    [maxwell-lte.kicad_pcb]
2018-10-14 Give a direct link to PWRKEY from the level converter in case my bootstrapping strategy is unworkable.
    [maxwell-lte.kicad_pcb, maxwell-lte.sch]
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2018-10-17 Updating to v1.4; adds output capacitor to onboard regulator; adds status input to level shifter.
    [maxwell-lte.kicad_pcb, maxwell-lte.sch]
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2018-10-21 Do not skip enablement steps if LTE is already powered.
    [lte.cpp]
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2018-10-22 Updating hardware to reference the proper libraries; adding new parts to board to support switching from dynamo input to battery.
    [maxwell.kicad_pcb, maxwell.sch, microcontroller.sch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]
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2018-10-31 Fixing speed calculation/refresh callbacks; adding new 'halloween' led preset.
    [menu.cpp]
2018-11-04 Fixing a bug that caused FIFO to be disabled.
    [SC16IS750.cpp, SC16IS750.h]
2018-11-04 Removing AdafruitFONA now that I've swapped to Arduino-Async-Modem.
    [SIM7000 Shield v4.brd, SIM7000 Shield v4.sch, SIM7000 Shield v5.brd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]
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2018-11-05 Fixing a bug that caused the device to hang immediately after posting status.
    [lte.cpp]
2018-11-06 Fixing misc can and status+lte related bugs.
    [lte.cpp, power.cpp, serial_commands.cpp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]
2018-11-09 Fixing status report name collision; removing obsolete menu items; adding new menu item for LTE enable/disable.
    [menu.cpp, serial_commands.cpp, status.cpp]
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2018-12-02 Minor updates to mak certain pads slightly larger.
    [maxwell.kicad_pcb, power.sch]
2018-12-04 Switch to using diode drop instead of a voltage divider for controlling min battery power.
    [maxwell.kicad_pcb, power.sch]
2018-12-27 Revision 1.6; switches to using an battery management IC for safety; adds better analog grounding.
    [maxwell.kicad_pcb, maxwell.sch, microcontroller.sch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]
2018-12-27 Better SOT-563-LargePads; connect all IDC connector pins on both layers.
    [maxwell.kicad_pcb]
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2019-01-08 Updating PWR board to v1.7; adds:
    * Fix for footprint of AP9101C (I have the five-pin package; not six)
    * Grounding VM on the AP9101C to BAT- to disable current protection;
    I'm using the TPS2113A for current protection, so this feature isn't
    needed.
    * Adds I2C-addressable INA219AID current sensor IC.
    * Adds I2C-addressable PCF8593 counter for speed measurement.
    [maxwell.kicad_pcb, maxwell.sch, microcontroller.sch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]
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2019-01-15 Final software fixes for ?1.7.
    [bluetooth.cpp, main.cpp, pin_map.h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]
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2019-01-20 Fixing power source CANbus announcement; adding stats message for console display.
    [power.cpp]
2019-01-20 Adding shortcut for disabling lighting via preset 0.
    [led_cycles.h, main.cpp]
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2019-01-23 Adding bluetooth icons; fixing button handling to be saner.
    [display.cpp, main.cpp]
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2019-01-23 Swapping fonts; helvR12 was a little too faint to make out while riding.
    [display.h]
2019-01-25 Adding new dynamo regulator board; efficiency of a linear regualator should be fine enough given how much voltage I'm working with.
    [maxwell-dynamo-regulator.kicad_pcb, maxwell-dynamo-regulator.sch]
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2019-02-02 Revision 1.8a
    * Collects regulated dynamo voltage via ADC channel 0.
    * Swaps default power source from VBATT to VDYNAMO. When charging, the
    battery may have exactly the same voltage as the dynamo due to voltage
    pulldown. During such a scenario, we should use the dynamo.
    * Adds previously missing pulldown resistor for open drain speed
    input.
    [maxwell.kicad_pcb, power.sch]
2019-02-03 Updating getPowerSource to match v1.8a (v1.7 board is updated to swap TPS2113 VIN1 with VIN2.
    [power.cpp]
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2019-02-04 Fixing button behavior; adding menu timeout controls.
    [display.cpp, display.h, main.cpp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]
2019-02-15 Updating to 1.8b; re-assigns power sources-to-TPS chip reverting earlier changes.
    [maxwell.kicad_pcb, power.sch]
2019-02-17 Revision 1.9a
    * Separates PCB into three boards (from two); adding a new
    'Rectifier' board mounted directly to the 'Power' board via a
    board-to-board connector.
    * Switches to active rectification.
    * Provide 5V directly to the battery; drop VCC voltage to
    4.3V via a diode drop.
    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
    [maxwell.kicad_pcb, maxwell.sch, microcontroller.sch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]
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2019-02-18 Missing connection from diode controller to VDYN+; bodged.
    [maxwell.kicad_pcb, maxwell.sch, rectification.sch]
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2019-02-23 Fixing errata:
    * Connecting ESP32 to WAKE to ensure that the ESP32 can keep
    the power on while doing things like flashing the uC.
    * Pull power button high to VCC via a diode instead of
    3V3 which is the very thing the power button will be
    turning on.
    * Updating sense resistor to 100mOhm instead of 20mOhm.
    [maxwell.kicad_pcb, maxwell.sch, power.sch]
2019-02-25 Maxwell Remote v2.0
    * Adds WAKE-controlled power switch to save power while sleeping.
    * Uses pin headers for connecting upper and lower layers instead
    of FPC connectors.
    [maxwell-remote-2.kicad_pcb, maxwell-remote-2.sch, maxwell-remote.kicad_pcb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]
2019-02-25 Maxwell Remote v2.0.1
    * Adds support for power-on by pressing handlebar button.
    The earlier design relied on the microcontroller waking
    when the button was pressed, but in this new switch
    configuration the microcontroller won't even be powered
    while the device is asleep, so we need to hard-wire
    the power button to the WAKE line.
    [maxwell-remote.kicad_pcb, upper.sch]
2019-02-25 Maxwell Remote v2.0.2
    * Switches off power to SPI-connected devices when powered-down.
    [maxwell-remote.kicad_pcb, upper.sch]
2019-02-26 Maxwell Remote v2.0.3
    * Fixes schematic such that an N-Channel mosfet is used for
    controlling the GND side of the SPI expansion ports.
    [maxwell-remote.kicad_pcb, upper.sch]
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2019-02-28 Renaming MCP79412RTC instance to avoid conflict with STM32 built-in.
    [MCP79412RTC.cpp, MCP79412RTC.h]
2019-03-03 Fixing errata:
    * Adding 10k pulldown for ENABLE_DISPLAY (backlight control).
    * Adding 2u capacitor to PDOWN_PU to ensure WAKE is pulled high
    for long enough for the microcontroller to start.
    [maxwell-remote.kicad_pcb, maxwell-remote.sch, upper.sch]
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2019-03-04 Maxwell v1.9.1
    While sciencing earlier today, I narrowed down my surprisingly-high
    quiescent current problem to being how I've handled switching
    off the Neopixels and SPI-connected devices. Historicaly,
    those were switched using a low-side N-Channel MOSFET. With these
    changes, these will be switched via a high-side P-Channel MOSFET
    (itself controlled by an N-Channel MOSFET to ensure that the
    microcontroller isn't exposed to VCC).
    * Swaps Neopixel power-off device from low-side N-Channel MOSFET
    to P-Channel MOSFET controlled by an N-Channel MOSFET.
    * Swaps SPI power-off device from low-side N-Channel MOSFET
    to P-Channel MOSFET controlled by an N-Channel MOSFET.
    * Fixes a few erroneous r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
    [maxwell.kicad_pcb, maxwell.sch, microcontroller.sch]
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2019-03-13 Explicitly set pin mode for both inputs to non-inverted.
    [power.cpp]
2019-03-17 Fix: Removes weird pull-up-only-on-power-down for LEFT_A; instead just always pulls up LEFT_A.
    [maxwell-remote.kicad_pcb, upper.sch]
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2019-03-23 Fix bug preventing console log search from not always prepending a space to your search query.
    [serial_commands.cpp]
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2019-04-06 Maxwell v1.9.2
    Over the last month, I've melted the voltage cap zeners
    off of the rectifier board. This is not great; they serve
    an essential purpose in preventing the mosfets and active
    rectifiers behind it from being exposed to an overvoltage
    situation and burning out (which has happened to at least
    one mosfet).
    * Uses much bigger DO-201AE package through-hole diodes.
    These should be able to dissapate a lot more heat, and
    if they do heat up the solder enough to begin melting
    at least they won't be able to fall out of position.
    * Adds a P-Ch mosfet between the rectifier and capacitor;
    this should allow me to programmatically turn off the
    dynamo power source when I'm travelling ve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
    [maxwell.kicad_pcb, rectification.sch]
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2019-04-07 Maxwell Remote v1.9.3
    * Uses LT3086IR's SHDN pin instead of a separate mosfet.
    * Minor board layout and size changes.
    [maxwell.kicad_pcb, rectification.sch]
2019-04-12 Maxwell Remote v1.9.4
    It occurred to me that were I to turn off the
    regulator, the voltage would just have to be
    burned off in the Zener diodes because the dynamo
    will just ratchet the voltage up as high as it could.
    Really -- I should just use a triac to turn off
    the dynamo.
    * Adds a (default-enabled) triac for switching
    the dynamo on and off.
    [maxwell.kicad_pcb, rectification.sch]
2019-04-14 Maxwell Remote v1.9.5
    SSRs and Triacs each have voltage drops that are a significant
    fraction of how much voltage I have available; let's just use
    a latching relay instead.
    * Adds Latching relay (and bypass jumper) for allowing one to
    switch off/on the dynamo power source.
    [maxwell.kicad_pcb, rectification.sch]
2019-04-27 Maxwell v1.9.6
    Adapting main uC board such that it can serve for _both_ the
    remote and main sides. I'm printing a new case that can be mounted on
    the front rack of the bike instead of the rear; this would obviate the
    need for having two separate microcontrollers communicating over CAN.
    * Adds new DISP connector in place of SPI_C (currently unused).
    [maxwell.kicad_pcb, maxwell.sch, microcontroller.sch]
2019-04-27 Minor correction to rectification board; removing erroneous trace.
    [maxwell.kicad_pcb]
2019-04-27 Maxwell v1.9.7
    Forgot to add connectors for left/right control sets.
    * Adds connectors for LEFT_A/B and RIGHT_A/B
    [maxwell.kicad_pcb, maxwell.sch, microcontroller.sch]
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2019-05-11 Maxwell v1.9.9
    Revision of PWR board
    * Adds circuit for controlling relay turning rectifier on/off.
    * Removes power switch; I've decided that just sucking right out of
    the battery is fine, especially since the charging chip I'm using
    specifically suggests that's alright.
    * Adds TMP100 temperature sensor; mostly because I just happened to
    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
    [maxwell.kicad_pcb, power.sch]
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2019-05-14 Fixing GPS coordinate gathering.
    [bluetooth.cpp, pin_map.h, status.cpp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]
2019-05-17 Fixing WS2812B library such that it specifically selects the proper SPI bus.
    [WS2812B.cpp]
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2019-05-20 Fixing a bug in when I show the 'LTE busy' message.
    [lte.cpp, menu.cpp]
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2019-05-23 Correct logic used for showing LTE connection indicator on display
    [display.cpp]
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2019-05-23 Fixes bug in which I was not using the trip counter.
    [status.cpp]
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2019-05-26 Break alerts across multiple lines if they are too long to fit on a single line.
    [display.cpp]
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2019-05-27 Log something when a power failure has been detected.
    [status.cpp]
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2019-06-23 If saved latitude/longitude doesn't make sense; return zero.
    [status.cpp]
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2019-10-30 Maxwell-rect v 1.9.11; adds fixes for a couple minor oversights.
    [maxwell.kicad_pcb, rectification.sch]
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2019-11-03 Do not disable dynamo at night anymore; the switching regulator is so much more efficient that it doesn't matter.
    [status.cpp]
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
